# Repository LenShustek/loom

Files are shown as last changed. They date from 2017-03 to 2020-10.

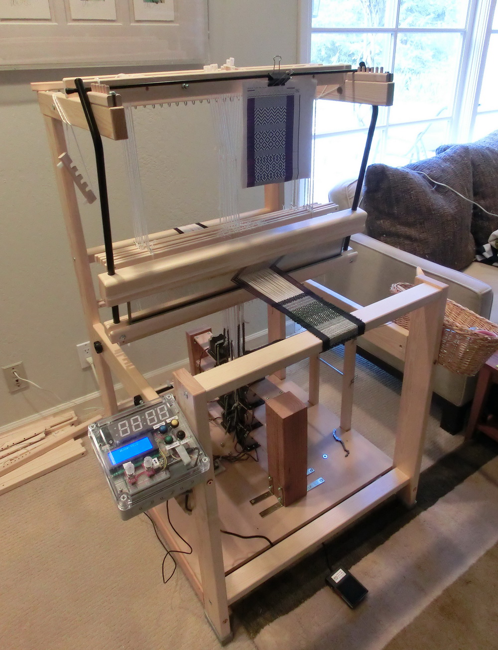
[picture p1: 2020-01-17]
small_weaving_test.JPG

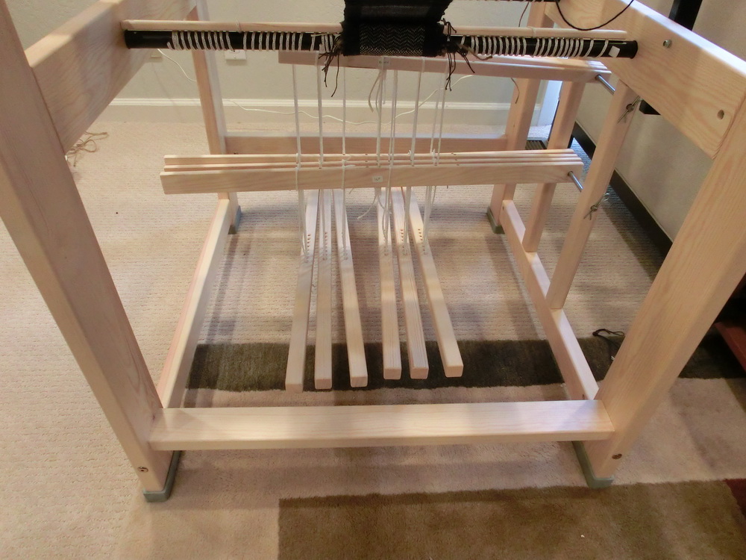
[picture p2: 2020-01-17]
treadles_and_lamms.JPG

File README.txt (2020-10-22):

eLoom: an automation system for the Glimakra "Julia" floor loom 

Tying up a loom with treadles and lamms is complicated, and so is the weaving. 
So I have replaced all the treadles and lamms in our Glimakra "Julia" 
countermarche floor loom with stepper motors that independently operate up to 
8 shafts. That not only makes setup and weaving easier, but it also allows 
patterns that would otherwise not be possible. 

The tie-ups and treadle sequences for up to 16 simulated treadles are 
graphically configured on a small screen. You then weave by throwing the 
shuttle and just pushing the single foot pedal to get the next configuration 
of the shafts. The warping, though, must still be done manually! 

For a one-minute video of it in action, see https://www.youtube.com/watch?v=ygZEDzQJMSk

The hardware added to the loom consists of:
 - up to 8 stepper motors, 23HS22-1504S, NEMA 23, 5.4V, 1.5A, 164 oz-in holding torque
 - up to 8 DRV8825 stepper motor drivers (Pololu or equiv.)
 - a 24VDC 200W power supply
 - 25-pitch sprockets and roller chain to connect the motors to the shaft lines
 - a control box that contains:
   - 1 4-row x 20-character LCD display (Adafruit 198)
   - 1 4-digit 7-segment I2C big digit numerical display (Adafruit 1268)
   - 2 rotary encoders with RGB LEDs and pushbuttons (Sparkfun COM-10982 and BOB-11722)
   - 4 general-purpose pushbuttons (MPJA 32730 or equiv.)
   - 1 attached foot pedal (MPJA 18150 or equiv.)
   - 1 Teensy 3.5 microprocessor, with 512KB flash, 192KB RAM, 4KB EEPROM, and 40 I/O pins
   
Len Shustek, January 2017

October 2020 update: After yeoman service for 3+ years, the plug-in breadboards with the
motor drivers started failing because the high current had deteriorated the contacts.
So I designed a proper printed circuit board replacement that is working great.
The design is in the motordriver subdirectory of this repository.

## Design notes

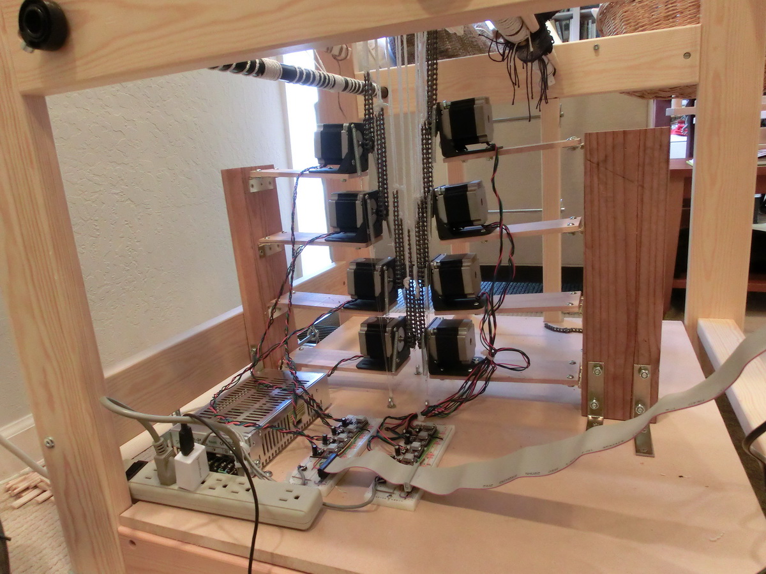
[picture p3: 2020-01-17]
stepper_motors.JPG

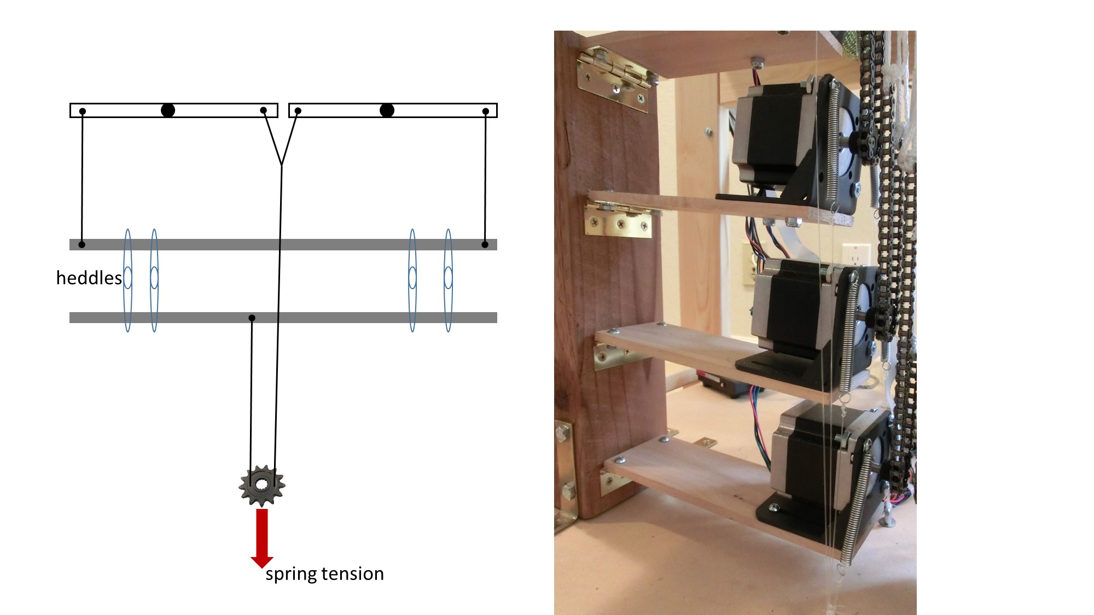
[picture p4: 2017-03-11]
countermarch_action_motorized.jpg

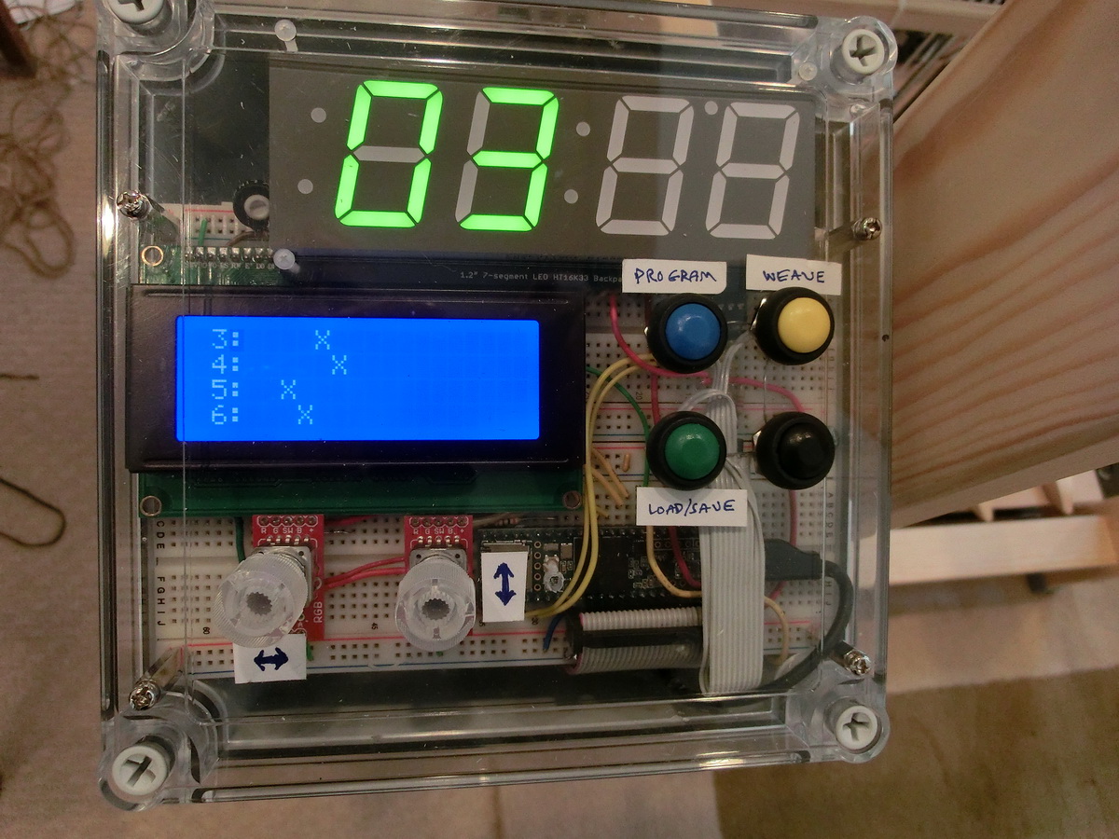
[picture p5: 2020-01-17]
control_box.JPG

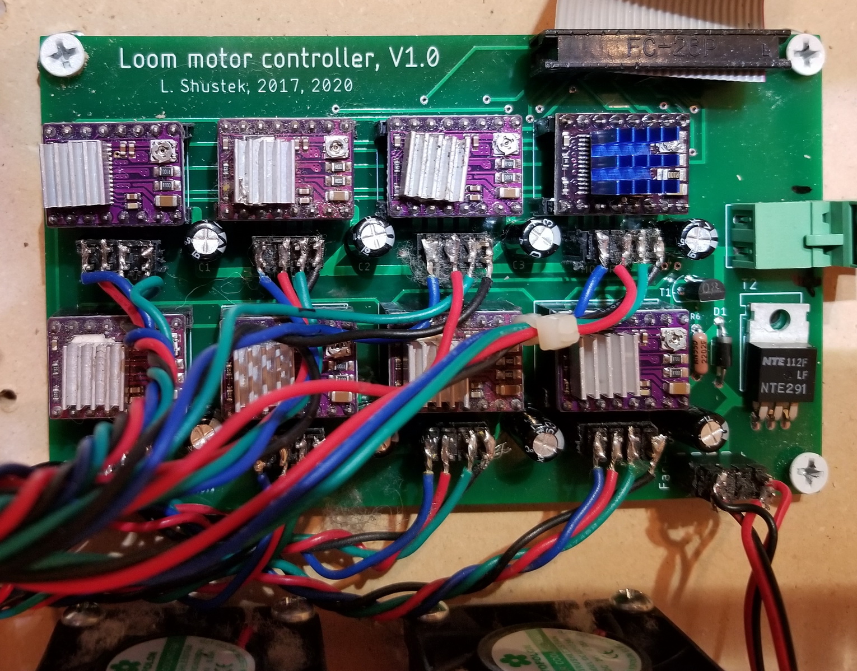
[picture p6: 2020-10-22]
motordriver/motordriver_board.jpg

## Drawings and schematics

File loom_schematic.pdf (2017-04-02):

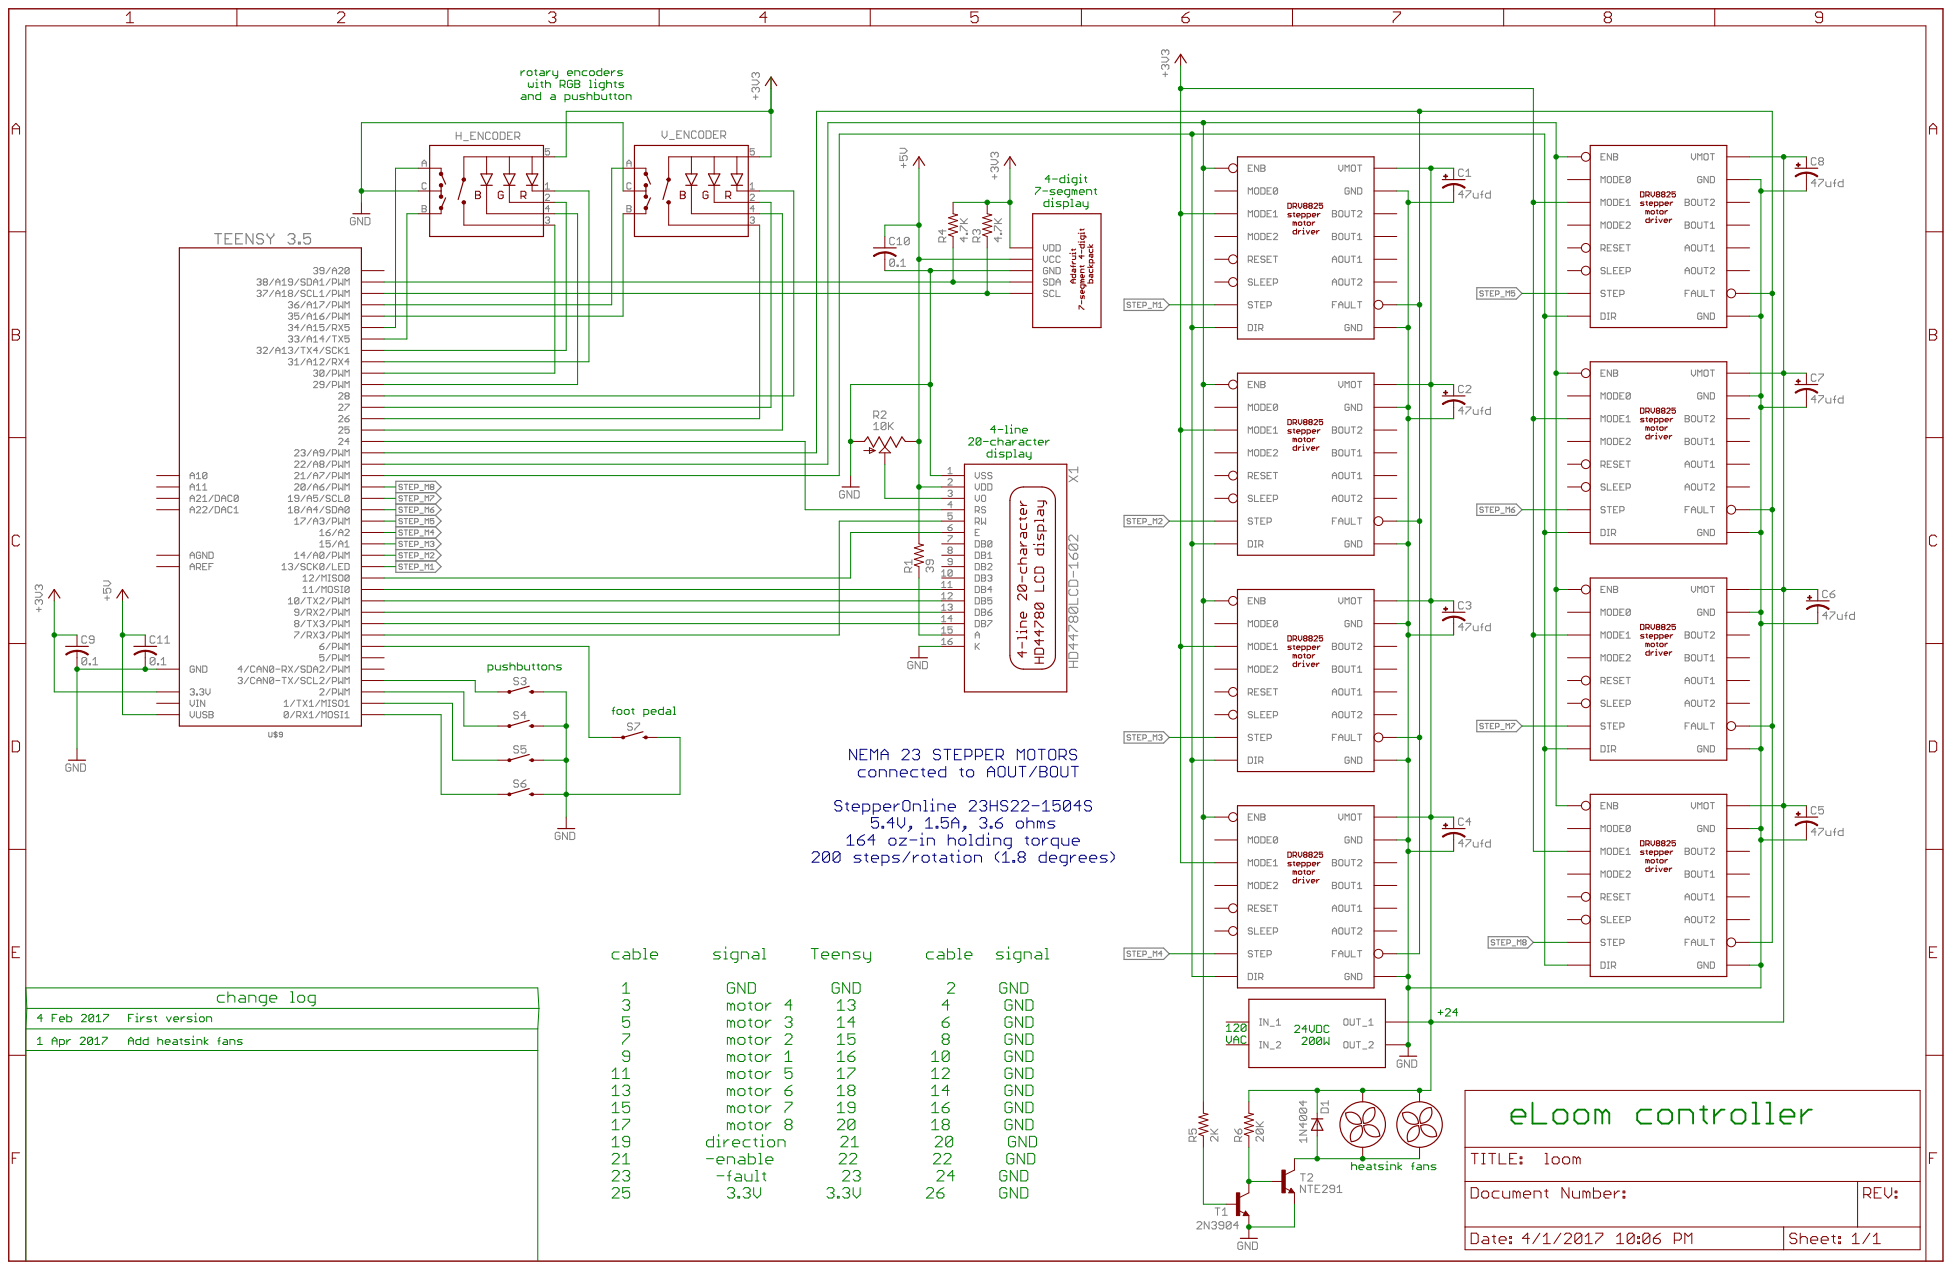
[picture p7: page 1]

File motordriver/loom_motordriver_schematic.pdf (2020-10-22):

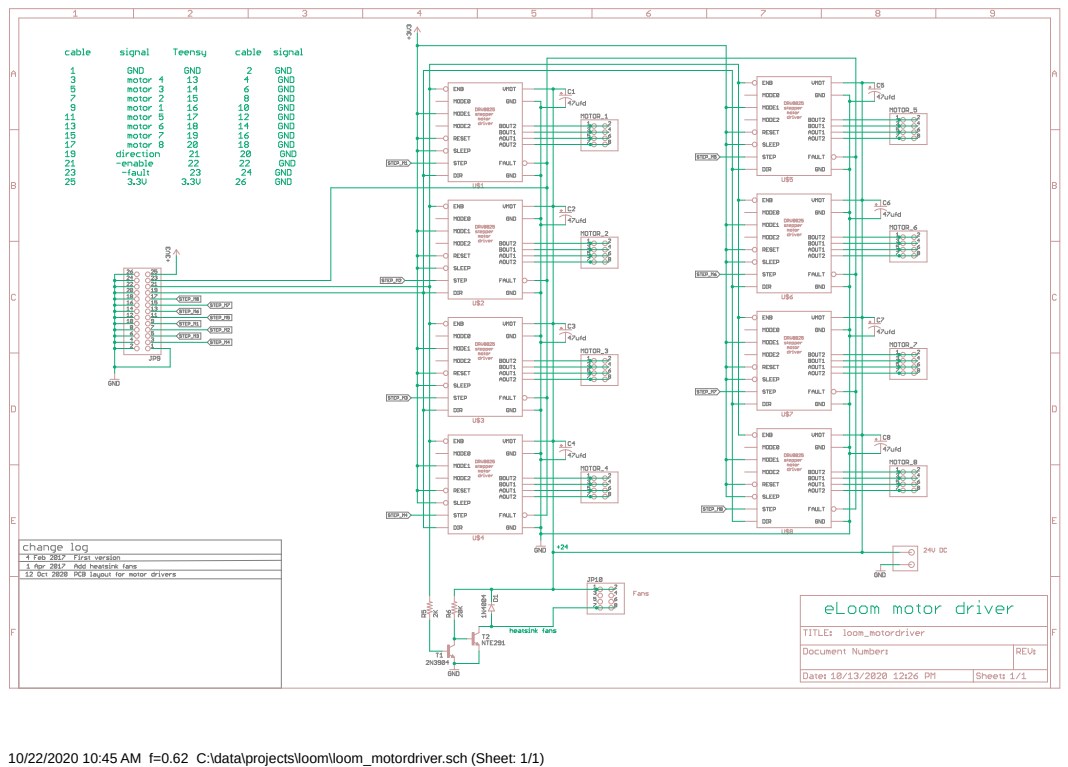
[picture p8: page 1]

10/22/2020 10:45 AM f=0.62 C:\data\projects\loom\loom_motordriver.sch (Sheet: 1/1)

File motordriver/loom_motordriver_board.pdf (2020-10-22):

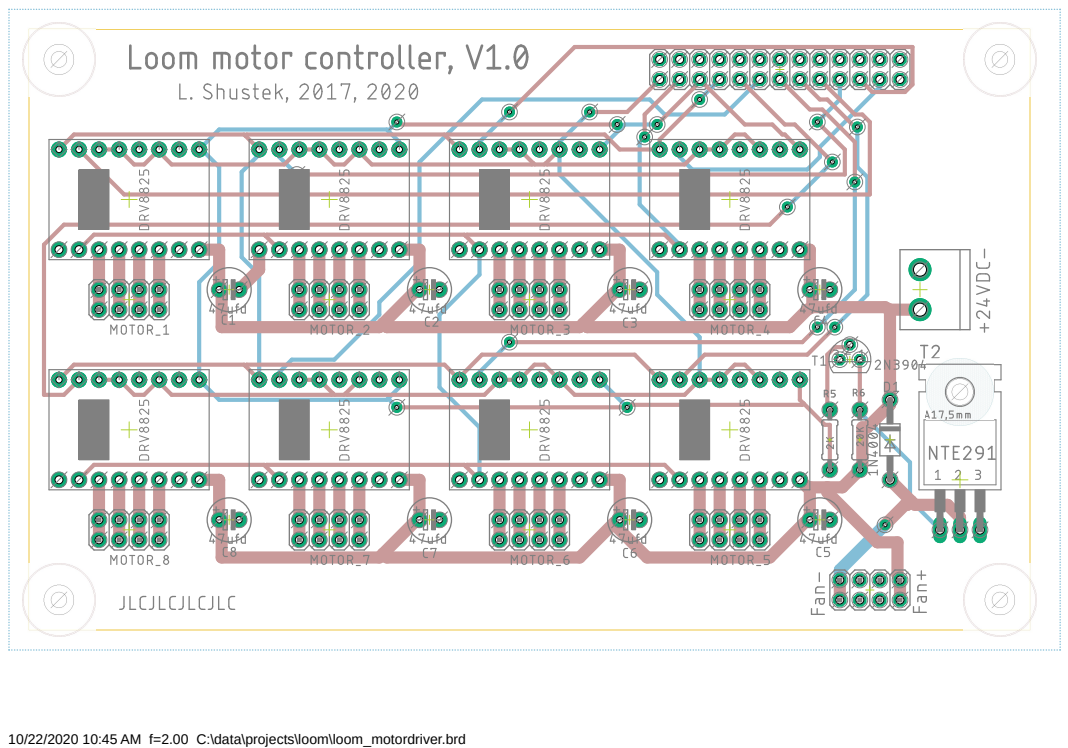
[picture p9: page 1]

10/22/2020 10:45 AM f=2.00 C:\data\projects\loom\loom_motordriver.brd

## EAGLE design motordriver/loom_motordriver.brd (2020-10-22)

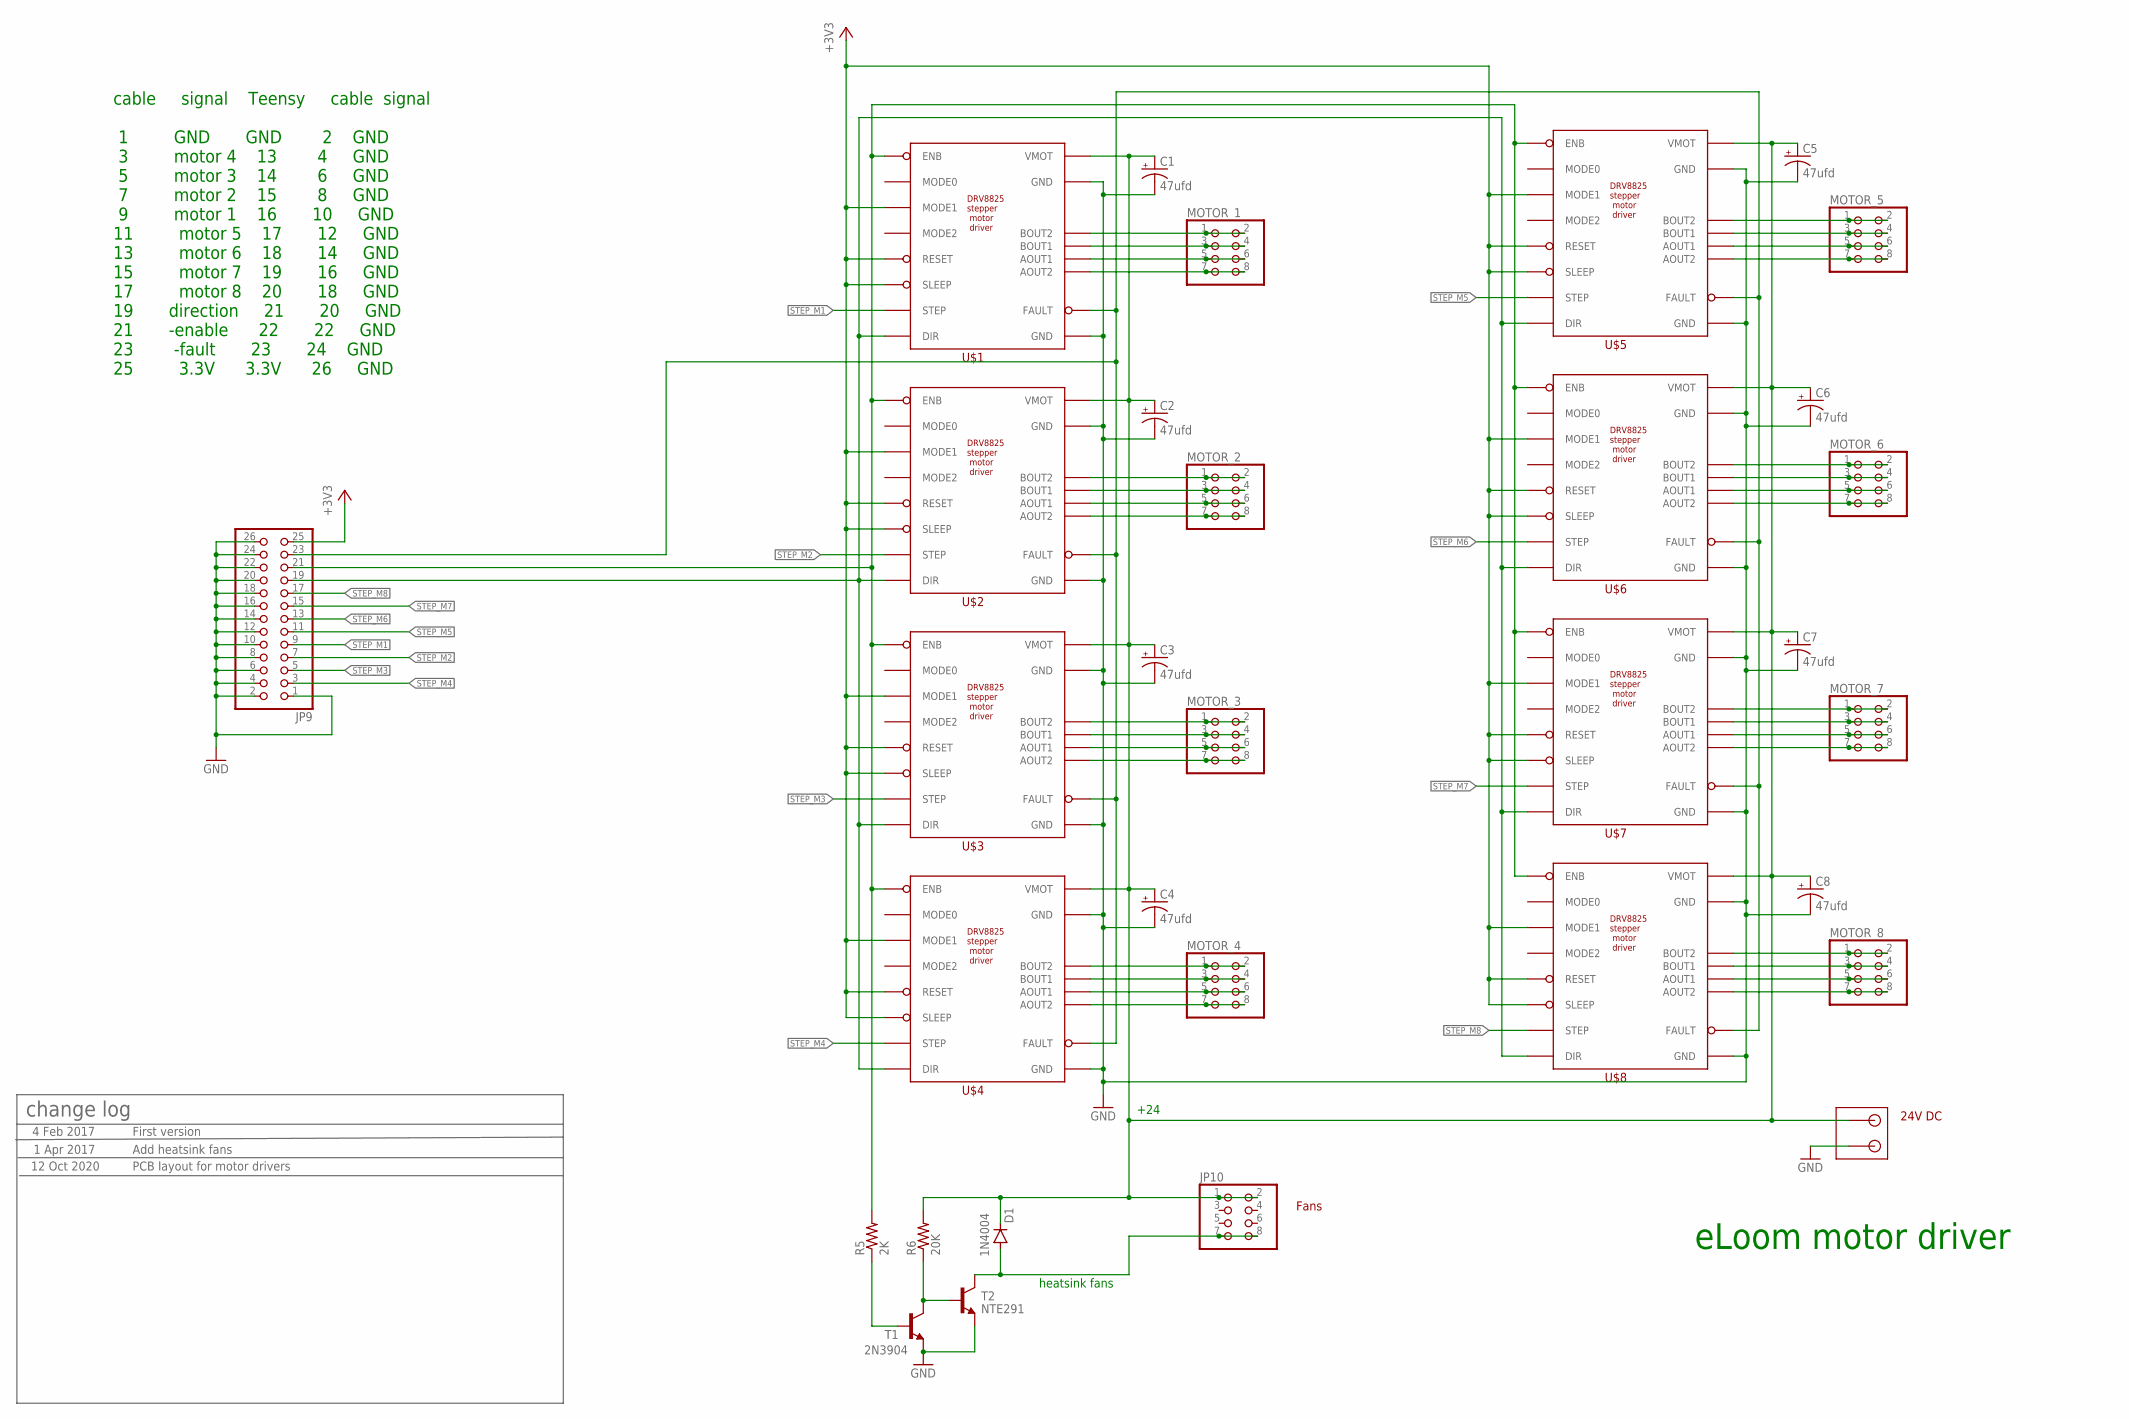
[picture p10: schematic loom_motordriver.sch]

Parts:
C1, C2, C3, C4, C5, C6, C7, C8: 47ufd; E2,5-6
D1: 1N4004; DO41-10
JP9: PINHD-2X13; 2X13
JP10: PINHD-2X4; 2X04
MOTOR_1, MOTOR_2, MOTOR_3, MOTOR_4, MOTOR_5, MOTOR_6, MOTOR_7, MOTOR_8: PINHD-2X4; 2X04
R5: 2K; 0204/7
R6: 20K; 0204/7
T1: 2N3904; TO92
T2: NTE291; TO220
U$1, U$2, U$3, U$4, U$5, U$6, U$7, U$8: DRV8825_STEPPER_MOTOR_DRIVER
U$9: CONNECTOR-2PIN; CONNECTOR-2PIN-5MM

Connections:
24V: C1.+, C2.+, C3.+, C4.+, C5.+, C6.+, C7.+, C8.+, D1.C, JP10.1, JP10.2, R6.2, U$1.P$16 (VMOT), U$2.P$16 (VMOT), U$3.P$16 (VMOT), U$4.P$16 (VMOT), U$5.P$16 (VMOT), U$6.P$16 (VMOT), U$7.P$16 (VMOT), U$8.P$16 (VMOT), U$9.P$1
+3V3: JP9.25, U$1.P$3 (MODE1), U$1.P$5 (RESET), U$1.P$6 (SLEEP), U$2.P$3 (MODE1), U$2.P$5 (RESET), U$2.P$6 (SLEEP), U$3.P$3 (MODE1), U$3.P$5 (RESET), U$3.P$6 (SLEEP), U$4.P$3 (MODE1), U$4.P$5 (RESET), U$4.P$6 (SLEEP), U$5.P$3 (MODE1), U$5.P$5 (RESET), U$5.P$6 (SLEEP), U$6.P$3 (MODE1), U$6.P$5 (RESET), U$6.P$6 (SLEEP), U$7.P$3 (MODE1), U$7.P$5 (RESET), U$7.P$6 (SLEEP), U$8.P$3 (MODE1), U$8.P$5 (RESET), U$8.P$6 (SLEEP)
DIR: JP9.19, U$1.P$8 (DIR), U$2.P$8 (DIR), U$3.P$8 (DIR), U$4.P$8 (DIR), U$5.P$8 (DIR), U$6.P$8 (DIR), U$7.P$8 (DIR), U$8.P$8 (DIR)
ENB: JP9.21, R5.2, U$1.P$1 (ENB), U$2.P$1 (ENB), U$3.P$1 (ENB), U$4.P$1 (ENB), U$5.P$1 (ENB), U$6.P$1 (ENB), U$7.P$1 (ENB), U$8.P$1 (ENB)
FAN: D1.A, JP10.7, JP10.8, T2.2 (C)
FAULT: JP9.23, U$1.P$10 (FAULT), U$2.P$10 (FAULT), U$3.P$10 (FAULT), U$4.P$10 (FAULT), U$5.P$10 (FAULT), U$6.P$10 (FAULT), U$7.P$10 (FAULT), U$8.P$10 (FAULT)
GND: C1.-, C2.-, C3.-, C4.-, C5.-, C6.-, C7.-, C8.-, JP9.1, JP9.2, JP9.4, JP9.6, JP9.8, JP9.10, JP9.12, JP9.14, JP9.16, JP9.18, JP9.20, JP9.22, JP9.24, JP9.26, T1.3 (E), T2.3 (E), U$1.P$9 (GND), U$1.P$15 (GND), U$2.P$9 (GND), U$2.P$15 (GND), U$3.P$9 (GND), U$3.P$15 (GND), U$4.P$9 (GND), U$4.P$15 (GND), U$5.P$9 (GND), U$5.P$15 (GND), U$6.P$9 (GND), U$6.P$15 (GND), U$7.P$9 (GND), U$7.P$15 (GND), U$8.P$9 (GND), U$8.P$15 (GND), U$9.P$2
unnamed: MOTOR_5.1, MOTOR_5.2, U$5.P$14 (BOUT2)
unnamed: MOTOR_5.3, MOTOR_5.4, U$5.P$13 (BOUT1)
unnamed: MOTOR_5.5, MOTOR_5.6, U$5.P$12 (AOUT1)
unnamed: MOTOR_5.7, MOTOR_5.8, U$5.P$11 (AOUT2)
unnamed: MOTOR_6.1, MOTOR_6.2, U$6.P$14 (BOUT2)
unnamed: MOTOR_6.3, MOTOR_6.4, U$6.P$13 (BOUT1)
unnamed: MOTOR_6.5, MOTOR_6.6, U$6.P$12 (AOUT1)
unnamed: MOTOR_6.7, MOTOR_6.8, U$6.P$11 (AOUT2)
unnamed: MOTOR_7.1, MOTOR_7.2, U$7.P$14 (BOUT2)
unnamed: MOTOR_7.3, MOTOR_7.4, U$7.P$13 (BOUT1)
unnamed: MOTOR_7.5, MOTOR_7.6, U$7.P$12 (AOUT1)
unnamed: MOTOR_7.7, MOTOR_7.8, U$7.P$11 (AOUT2)
unnamed: MOTOR_8.1, MOTOR_8.2, U$8.P$14 (BOUT2)
unnamed: MOTOR_8.3, MOTOR_8.4, U$8.P$13 (BOUT1)
unnamed: MOTOR_8.5, MOTOR_8.6, U$8.P$12 (AOUT1)
unnamed: MOTOR_8.7, MOTOR_8.8, U$8.P$11 (AOUT2)
unnamed: MOTOR_1.1, MOTOR_1.2, U$1.P$14 (BOUT2)
unnamed: MOTOR_1.3, MOTOR_1.4, U$1.P$13 (BOUT1)
unnamed: MOTOR_1.5, MOTOR_1.6, U$1.P$12 (AOUT1)
unnamed: MOTOR_1.7, MOTOR_1.8, U$1.P$11 (AOUT2)
unnamed: MOTOR_2.1, MOTOR_2.2, U$2.P$14 (BOUT2)
unnamed: MOTOR_2.3, MOTOR_2.4, U$2.P$13 (BOUT1)
unnamed: MOTOR_2.5, MOTOR_2.6, U$2.P$12 (AOUT1)
unnamed: MOTOR_2.7, MOTOR_2.8, U$2.P$11 (AOUT2)
unnamed: MOTOR_3.1, MOTOR_3.2, U$3.P$14 (BOUT2)
unnamed: MOTOR_3.3, MOTOR_3.4, U$3.P$13 (BOUT1)
unnamed: MOTOR_3.5, MOTOR_3.6, U$3.P$12 (AOUT1)
unnamed: MOTOR_3.7, MOTOR_3.8, U$3.P$11 (AOUT2)
unnamed: R5.1, T1.2 (B)
unnamed: R6.1, T1.1 (C), T2.1 (B)
unnamed: MOTOR_4.1, MOTOR_4.2, U$4.P$14 (BOUT2)
unnamed: MOTOR_4.3, MOTOR_4.4, U$4.P$13 (BOUT1)
unnamed: MOTOR_4.5, MOTOR_4.6, U$4.P$12 (AOUT1)
unnamed: MOTOR_4.7, MOTOR_4.8, U$4.P$11 (AOUT2)
STEP_M1: JP9.9, U$1.P$7 (STEP)
STEP_M2: JP9.7, U$2.P$7 (STEP)
STEP_M3: JP9.5, U$3.P$7 (STEP)
STEP_M4: JP9.3, U$4.P$7 (STEP)
STEP_M5: JP9.11, U$5.P$7 (STEP)
STEP_M6: JP9.13, U$6.P$7 (STEP)
STEP_M7: JP9.15, U$7.P$7 (STEP)
STEP_M8: JP9.17, U$8.P$7 (STEP)

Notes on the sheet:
eLoom motor driver
cable signal Teensy cable signal 1 GND GND 2 GND 3 motor 4 13 4 GND 5 motor 3 14 6 GND 7 motor 2 15 8 GND 9 motor 1 16 10 GND 11 motor 5 17 12 GND 13 motor 6 18 14 GND 15 motor 7 19 16 GND 17 motor 8 20 18 GND 19 direction 21 20 GND 21 -enable 22 22 GND 23 -fault 23 24 GND 25 3.3V 3.3V 26 GND
heatsink fans
+24
change log
4 Feb 2017
First version
1 Apr 2017
Add heatsink fans
24V DC
Fans
12 Oct 2020
PCB layout for motor drivers

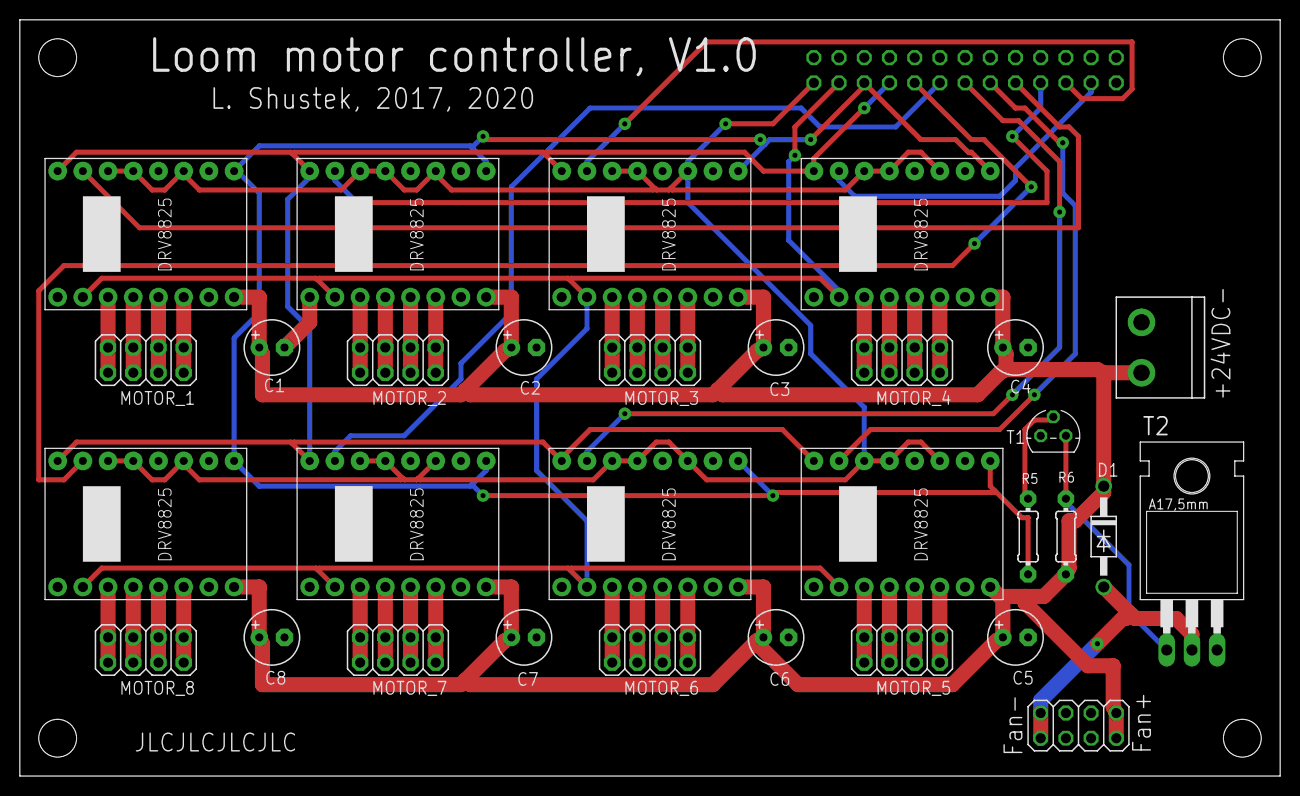
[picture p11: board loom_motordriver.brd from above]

Board: 2 copper layers, 127.0 x 76.2 mm, 32 parts (1 on the bottom side), 49 nets.

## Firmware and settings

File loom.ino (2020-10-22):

/******************************************************************************************************

   automation program for the Glimakra "Julia" floor loom

   The hardware added to the loom consists of:
    - up to 8 stepper motors, 23HS22-1504S, NEMA 23, 5.4V, 1.5A, 164 oz-in holding torque
    - up to 8 DRV8825 stepper motor drivers (Pololu or equiv.)
    - 1 24VDC 200W power supply
    - 1 4-row x 20-character LCD display (Adafruit 198)
    - 1 4-digit 7-segment I2C big digit numerical display (Adafruit 1268)
    - 2 rotary encoders with RGB LEDs and pushbuttons (Sparkfun COM-10982 and BOB-11722)
    - 4 general-purpose pushbuttons (MPJA 32730 or equiv.)
    - 1 foot pedal (MPJA 18150 or equiv.)
    - 1 Teensy 3.5 microprocessor, with 512KB flash, 192KB RAM, 4KB EEPROM, and 40 I/O pins

   The software allows you to graphically configure the treadle tie-ups and the treadle sequence,
   and then weave by throwing the shuttle and just pushing the single foot pedal to get the
   next configuration of the shafts.  The warping, though, must still be done manually!

   See https://github.com/LenShustek/loom for more information about this project.

   When you install a DRV8825 stepper motor driver, adjust the pot on the board so that
   there is 0.75V at the body of the pot, which is for 1.5A drive current to the motor.
   The motor doesn't have to be on when you that.

   ------------------------------------------------------------------------------------------------------
   Copyright (c) 2017, Len Shustek

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
   THE SOFTWARE IS PROVIDED "AS IS", WITHOUT WARRANTY OF ANY KIND, EXPRESS OR IMPLIED, INCLUDING BUT
   NOT LIMITED TO THE WARRANTIES OF MERCHANTABILITY, FITNESS FOR A PARTICULAR PURPOSE AND
   NONINFRINGEMENT. IN NO EVENT SHALL THE AUTHORS OR COPYRIGHT HOLDERS BE LIABLE FOR ANY CLAIM,
   DAMAGES OR OTHER LIABILITY, WHETHER IN AN ACTION OF CONTRACT, TORT OR OTHERWISE, ARISING
   FROM, OUT OF OR IN CONNECTION WITH THE SOFTWARE OR THE USE OR OTHER DEALINGS IN THE SOFTWARE.
   ------------------------------------------------------------------------------------------------------

******************************************************************************************************/
/*
   23 Jan 2017, L. Shustek, V1.0, - first version
   31 Jan 2017, L. Shustek, V1.1, - fix treadle sequence changes during weaving
                                  - clean up filename handling and display
    4 Feb 2017, L. Shustek, V1.2  - add motor fault detection
                                  - fix filename bug
                                  - change schematic to match driver physical layout
                                  - clean up compiler warnings
   10 Feb 2017, L. Shustek, V1.3  - separate motor hardware config, and don't write it to memory
                                  - better debugging output
                                  - parametrize CW/CCW motor initialization
                                  - highlight the treadle while weaving, not just the line
   12 Feb 2017, L. Shustek, V1.4  - more interesting light show during weaving
                                  - make the vertical button during weaving be "undo" to the previous shed
                                  - allow abort from load/save/erase menu
   23 Mar 2017, L. Shustek, V1.5  - increase max treadle sequence to 99
                                  - fix bug when editing the filename extends its length
                                  - temporarily disable motors during weaving if there is no activity for a few minutes
   27 Mar 2017, L. Shustek, V1.6  - display filename on top-level screen, or "unsaved" if pgmg changes are made
                                  - default to current file in load/save menu
                                  - exit from program mode if any other button is pushed
   15 Jun 2017, L. Shustek, V1.7  - fix bug: exiting weaving mode after motors had timed out didn't return
                                    the shafts to the neutral position
    8 Jan 2018, L. Shustek, V1.8  - change "zero" button to "backup" button in weave mode
                                  - display frame numbers instead of X on the tieup screen
                                  - display treadle numbers instead of X on the treadle sequence screen
                                  - fix bug: backing up weave at the first treadle position failed
   28 Oct 2018, L. Shustek, V1.9  - add an option to do "Tabby" between each step of a treadle sequence
                                    if the first two treadles are otherwise unused
    3 Jan 2019, L. Shustek, V1.10 - during calibration, show the distance the frame moves
                                  - add a file option to reverse the fabric by inverting the tieups
   13 Jun 2020, L. Shustek, V1.11 - fix bug: "alternate tabby" wasn't working for shafts other than 0 and 1
                                  - fix bug: always set FILE_TABBY one way or the other when changing programming
   10 Oct 2020, L. Shustek, V1.12 - allow "weave" button to abort the calibration process
                                  - during calibration, show the previously set calibration point
                                  - increase debounce delay because our switches are really noisy

*/
#define VERSION "1.12"

/***** Enhancement ideas:

    - Invent a more programmatic way to configure treadle sequences with repeat loops.
      Since weaving is limited to one treadle at a time we can use decimal rather than unary
      notation on the narrow display. It doesn't match weaving books, though, so weavers would
      consider that sacrilegious!

      Idea #1: a programming mode for "treadle loops", in addition to the traditional sequence.
      The notation might be like this, using "Irish Meadows blanket" as an example:
          4x: 5 6
          6x: 6 5
          8x: 5 6
          ?x: 1 2 3 4
          8x: 5 6
          6x: 6 5
          4x: 5 6
      When weaving, the "?x" line would be repeated indefinitely until a button is pushed to advance.
      Either this "treadle loop" notation or a reconstructed "treadle sequence" notation could be displayed.
      The 3rd and 4th numbers on the big-digit display could show how far along in a repeat sequence we are.
      The file format would have to be elaborated to save and load these looped treadle sequences.

    - Save space by making the tieup[][] matrix be a true bitmap. That would allow more files in the EEPROM.
      Or instead: use an SD card for files, and to hell with optimizing the size to fit in the 4K EEPROM!
*/

#define DEBUG false
#define HW_TEST false

#include <Encoder.h>
#include <LiquidCrystalFast.h>
#include <EEPROM.h>
#include <i2c_t3.h>
#include <string.h>

//**** global parameters

// All stored files will break if NUM_TREADLES, NUM_SHAFTS, or MAX_SEQUENCE is changed!
#define NUM_TREADLES 16 // max 17 will fit on the display currently
#define NUM_SHAFTS 8
#define MAX_SEQUENCE 99

#define MSEC_PER_ROTATION 1000      // how long we should take for one rotation
#define uSTEPS_PER_STEP 4           // how many microsteps per step the drivers are configured for (MODE1 high)
#define STEPS_PER_ROTATION (200 * uSTEPS_PER_STEP)  // the stepper motors have 1.8 degree "full" steps; 360/1.8=200
#define HUNDRETHINCHES_PER_ROTATION ((int)(0.75*3.14*100.0+0.5))  // we use a 3/4" drive gear
#define MIN_STEP_uSEC (1000UL * MSEC_PER_ROTATION / STEPS_PER_ROTATION)
#define DEBOUNCE_MSEC 100
#define ROTATION_PERCENT (130/2) // what part of a full rotation goes from CENTER to UP or DOWN, nominally
#define STEPS_PER_LIGHT_CHANGE 64
#define MINS_BEFORE_MOTOR_DISABLE 10

//**** hardware pin configuration

#define LCD_D4 11  // Hitachi HD44780 LCD controller
#define LCD_D5 10
#define LCD_D6 9
#define LCD_D7 8
#define LCD_ENB 12
#define LCD_RS 24
#define LCD_RW 7
#define PB1 3  // pushbuttons: active low (blue)
#define PB2 2  //   (yellow)
#define PB3 1  //   (green)
#define PB4 0  //   (black)
#define PEDAL 6
#define MOTOR_DIR 21    // direction control for all motors
#define MOTOR_ENB 22    // active low: enable motors
#define MOTOR_FAULT 23  // active low input: motor fault
#define H_ENC_RED 31    // horizontal and vertical rotary encoder lights
#define H_ENC_GREEN 32  //   (active low)
#define H_ENC_BLUE 29
#define V_ENC_RED 28
#define V_ENC_GREEN 27
#define V_ENC_BLUE 25
#define LED_ON LOW
#define LED_OFF HIGH
#define H_ENC_PB 30     // encoder pushbuttons: active high
#define V_ENC_PB 26
#define H_ENC_A 34      // encoder step outputs
#define H_ENC_B 33
#define V_ENC_A 36
#define V_ENC_B 35
#define ENCODER_INCR 4  // number of encoder steps per click
#define LED_SCL 37      // SCL1 for the big 4-digit 7-segment LED display (Wire1)
#define LED_SDA 38      // SDA1 for the big 4-digit 7-segment LED display (Wire1)
#define I2C_ADDR 0x70   // default I2C slave address
// unused Teensy 3.5 pins: 4, 5, 39

enum events { // input events
   eNone,
   ePB1, ePB2, ePB3, ePB4,  // big pushbuttons: program, weave, load/save, unweave
   ePBH, ePBV,              // horizontal and vertical encoder pushbuttons
   ePEDAL,                  // foot pedal
   eHrotL, eHrotR,          // horizontal encoder rotation
   eVrotL, eVrotR           // vertical encoder rotation
};
static struct {   // input pins
   byte pin;
   enum events event;
   byte active_state; }
inpins[] = {
   {PB1, ePB1, LOW },
   {PB2, ePB2, LOW },
   {PB3, ePB3, LOW },
   {PB4, ePB4, LOW },
   { H_ENC_PB, ePBH, HIGH },
   { V_ENC_PB, ePBV, HIGH },
   {PEDAL, ePEDAL, LOW },
   {0xff } };

static byte lightpins[] = { // output pins for encoder LEDs
   H_ENC_RED, H_ENC_GREEN, H_ENC_BLUE,
   V_ENC_RED, V_ENC_GREEN, V_ENC_BLUE, 0xff };

static struct  { // output pins for the stepper motors
   byte pin_step;       // what pin starts a step for this motor
   bool clockwise;      // is clockwise up?
#define FRONT_CW false  // (these depend on which way the chains are
#define BACK_CW true    //  looped around the sprockets)
} shaft_hardware[NUM_SHAFTS] = {
   {16, FRONT_CW }, // top front motor
   {15, FRONT_CW },
   {14, FRONT_CW },
   {13, FRONT_CW }, // bottom front motor
   {17, BACK_CW },  // bottom back motor
   {18, BACK_CW },
   {19, BACK_CW },
   {20, BACK_CW }   // top back motor
};

enum shaft_positions {SHAFT_CENTER, SHAFT_UP, SHAFT_DOWN };
#define NOMINAL_STEPS ((ROTATION_PERCENT * STEPS_PER_ROTATION) / 100)
static struct {
   enum shaft_positions shaft_position;  // where is the shaft currently?
   int steps_to_down;   // how many steps move from center to down
   int steps_to_up;     // how many steps move from center to up
   int steps_to_move;   // how many steps up (pos) or down (neg) are left to move
}
shaft_status[NUM_SHAFTS] = {
   {SHAFT_CENTER,  NOMINAL_STEPS,  NOMINAL_STEPS, 0 },  // top front motor
   {SHAFT_CENTER,  NOMINAL_STEPS,  NOMINAL_STEPS, 0 },
   {SHAFT_CENTER,  NOMINAL_STEPS,  NOMINAL_STEPS, 0 },
   {SHAFT_CENTER,  NOMINAL_STEPS,  NOMINAL_STEPS, 0 },  // bottom front motor
   {SHAFT_CENTER,  NOMINAL_STEPS,  NOMINAL_STEPS, 0 },  // bottom back motor
   {SHAFT_CENTER,  NOMINAL_STEPS,  NOMINAL_STEPS, 0 },
   {SHAFT_CENTER,  NOMINAL_STEPS,  NOMINAL_STEPS, 0 },
   {SHAFT_CENTER,  NOMINAL_STEPS,  NOMINAL_STEPS, 0 }   // top back motor
};

// weaving configuration

static bool tieup [NUM_SHAFTS] [NUM_TREADLES] =  { // does shaft i go down with treadle j?
   // initialization: a line is all treadles connected to a particular shaft
   {1, 0, 0, 0, 0, 0, 0, 0, 0, 0, 0, 0, 0, 0, 0, 0 }, // initialized to basic weave
   {0, 1, 0, 0, 0, 0, 0, 0, 0, 0, 0, 0, 0, 0, 0, 0 },
   /* everything else is 0 */
};
static byte treadle_sequence[MAX_SEQUENCE]; // treadle sequence for this pattern; values are 0..NUM_TREADLES-1
#define UNUSED_SEQ 0xff                     // or 0xff signifying "this position is unused"
static int sequence_size;

//**** EEPROM format for persistent data

#define EEPROM_SIZE 4096
/* layout in the EEPROM is:
     config_hdr
     shaft_status []
     repeat for each file {
        file_hdr
        tieup []
        treadle_sequence []
        }
*/
struct {
   char id[4];       // "cfg" for identification
   int size;         // CONFIG_SIZE: size of the whole config record, including this header
   byte numshafts;   // compile-time config parameters for consistency checking
   byte numtreadles;
   byte maxsequence;
   byte lastfilenum;  // the last file we loaded or saved
   byte tr_seq_pos;   // the current index into the treadle sequence for that file
   byte tr_treadle;   // the current treadle (could be 0/1 for "alternate tabby" mode)
   byte unused[14];
   // after this we write the "shaft_status" array, which contains the current shaft configuration data
} config_hdr = {0 };
#define CONFIG_SIZE ((int)sizeof(config_hdr) + (int)sizeof(shaft_status))

#define MAX_FILENAME 14
struct {
   char id[4]; // "fil" for identification
   int16_t size;   // size of the whole file, including this header
   byte flags;
#define FILE_TABBY 0x01         // use Tabby 1/2 between each treadle step
#define FILE_INVERT_TIEUPS 0x02 // invert the top and bottom of the fabric
   byte unused;
   byte checksum;
   char filename[MAX_FILENAME + 1]; // null-terminated string
   // after this we write the tieup array, followed by the treadle_sequence vector
} file_hdr;
#define FILE_SIZE ((int)sizeof(file_hdr) + (int)sizeof(tieup) + (int)sizeof(treadle_sequence))
#define MAX_FILES ((EEPROM_SIZE - CONFIG_SIZE) / FILE_SIZE)
// The current implementation assumes all files are padded to the fixed maximum size.
// All stored files will break if NUM_SHAFTS, NUM_TREADLES, or MAX_SEQUENCE is changed!

//    other global variables

LiquidCrystalFast lcd (LCD_RS, LCD_RW, LCD_ENB, LCD_D4, LCD_D5, LCD_D6, LCD_D7);
Encoder H_ENC (H_ENC_A, H_ENC_B);
Encoder V_ENC (V_ENC_A, V_ENC_B);
long Hold, Vold;  // last encoder values
#define ENC_STEPS_PER_CLICK 4
char last_filename[MAX_FILENAME + 1] = {0};
bool unsaved_file = false;

//***********************************************************************
//    utility routines
//***********************************************************************

void assert (boolean test, const char *msg) {
   if (!test) {
      lcd.clear(); lcd.print("** INTERNAL ERROR **");
      lcd.setCursor(0, 1); lcd.print("Assertion failed:");
      lcd.setCursor(0, 2); lcd.print(msg);
      while (true) ; } }

void center_message (byte row, const char *msg) {
   int len, nblanks;
   len = strlen(msg);
   assert (len <= 20, "bad center_message");
   nblanks = (20 - len) >> 1;
   lcd.setCursor(0, row);
   for (byte i = 0; i < nblanks; ++i) lcd.print(" ");
   lcd.print(msg);
   nblanks = (20 - nblanks) - len;
   for (byte i = 0; i < nblanks; ++i) lcd.print(" "); }

void info_message(const char *msg1, char *msg2) {
   lcd.clear(); center_message(1, msg1);
   if (msg2) center_message(2, msg2);
   delay(3000);
   lcd.clear(); }

void wait_for_button(byte pin) {
   while (digitalRead(pin) == HIGH) ;
   delay(DEBOUNCE_MSEC);
   while (digitalRead(pin) == LOW) ;
   delay(DEBOUNCE_MSEC); }

void testbutton (byte pin, bool active) {
   if (digitalRead(pin) == active) {
      Serial.print("pushed: "); Serial.println(pin);
      delay(DEBOUNCE_MSEC);
      while (digitalRead(pin) == active) ;
      Serial.print("release: "); Serial.println(pin);
      delay(DEBOUNCE_MSEC); } }

void H_LED (int led) {
   digitalWrite(H_ENC_RED, led == H_ENC_RED ? LED_ON : LED_OFF);
   digitalWrite(H_ENC_GREEN, led == H_ENC_GREEN ? LED_ON : LED_OFF);
   digitalWrite(H_ENC_BLUE, led == H_ENC_BLUE ? LED_ON : LED_OFF); }
void V_LED (int led) {
   digitalWrite(V_ENC_RED, led == V_ENC_RED ? LED_ON : LED_OFF);
   digitalWrite(V_ENC_GREEN, led == V_ENC_GREEN ? LED_ON : LED_OFF);
   digitalWrite(V_ENC_BLUE, led == V_ENC_BLUE ? LED_ON : LED_OFF); }

//***********************************************************************
//     big 7-sgement LED display routines
//***********************************************************************

static const uint8_t numbertable[] = {
   0x3F, /* 0 */  0x06, /* 1 */  0x5B, /* 2 */  0x4F, /* 3 */  0x66, /* 4 */
   0x6D, /* 5 */  0x7D, /* 6 */  0x07, /* 7 */  0x7F, /* 8 */  0x6F, /* 9 */
   0x77, /* a */  0x7C, /* b */  0x39, /* C */  0x5E, /* d */  0x79, /* E */  0x71, /* F */
};
uint16_t displaybuffer[8];

void led7_turnoff(void) {
   Wire1.beginTransmission(I2C_ADDR);
   Wire1.write(0x80);  // turn off the display
   Wire1.endTransmission(); }

void led7_start(void) {
   Wire1.begin();    // start LED display
   Wire1.beginTransmission(I2C_ADDR);
   Wire1.write(0x21);  // turn on oscillator
   Wire1.endTransmission();
   Wire1.beginTransmission(I2C_ADDR);
   Wire1.write(0xef);  // set maximum brightness
   Wire1.endTransmission();
   led7_turnoff(); }

void led7_write_digit(byte pos, byte num, bool dot) {
   if (pos > 4) pos = 4;
   if (num > 15) num = 15;
   displaybuffer[pos] = numbertable[num] | (dot << 7); }

void led7_shownum(byte num, bool left) {
   led7_write_digit(left ? 0 : 3, (num / 10) % 10, false);
   led7_write_digit(left ? 1 : 4, num % 10, false);
   Wire1.beginTransmission(I2C_ADDR);
   Wire1.write((uint8_t)0x00); // start at address $00
   for (uint8_t i = 0; i < 8; i++) {
      Wire1.write(displaybuffer[i] & 0xFF);
      Wire1.write(displaybuffer[i] >> 8); }
   Wire1.endTransmission();
   Wire1.beginTransmission(I2C_ADDR);
   Wire1.write(0x81);  // turn on the display
   Wire1.endTransmission(); }

//****** more utility routines

void test_hardware(void) {
   for (int i = 0; lightpins[i] != 0xff; ++i) { // test all the lights
      digitalWrite(lightpins[i], LOW);
      delay(750);
      digitalWrite(lightpins[i], HIGH);
      delay(250); }
   for (int row = 0; row < 4; ++row) {  // test the LCD display
      char buf[21];
      sprintf(buf, "row %d", row);
      center_message(row, buf); }
   for (int leftright = 0; leftright < 2; ++leftright) {
      for (int i = 0; i < 10; ++i) { // test the LED display
         led7_shownum(i, leftright);
         delay(500); }
      for (int i = 0; i < 100; i += 10) {
         led7_shownum(i, leftright);
         delay(500); } }
   long Vold = -999, Hold = -999, Vnew, Hnew;
   while (1) {
      testbutton(PB1, LOW);
      testbutton(PB2, LOW);
      testbutton(PB3, LOW);
      testbutton(PB4, LOW);
      testbutton(PEDAL, LOW);
      testbutton(H_ENC_PB, HIGH);
      testbutton(V_ENC_PB, HIGH);
      Hnew = H_ENC.read();
      if (Hnew != Hold) {
         Serial.print("H pos: "); Serial.println(Hnew);
         Hold = Hnew; }
      Vnew = V_ENC.read();
      if (Vnew != Vold) {
         Serial.print("V pos: "); Serial.println(Vnew);
         Vold = Vnew; } } }

enum events check_event(void) {
   // check for a switch or button event; return eNone if none
   for (int i = 0; inpins[i].pin != 0xff; ++i) { //test all inputs
      // we should be cleverer here: trigger on press, but record to ignore until release
      if (digitalRead(inpins[i].pin) == inpins[i].active_state) { // button pushed
         delay(DEBOUNCE_MSEC);
         while (digitalRead(inpins[i].pin) == inpins[i].active_state) ;  // wait for release
         delay(DEBOUNCE_MSEC);
         return inpins[i].event; } }
   long Hnew = H_ENC.read();
   if (Hnew - Hold >= ENC_STEPS_PER_CLICK) {
      Hold = Hnew;
      return eHrotL; }
   if (Hold - Hnew >= ENC_STEPS_PER_CLICK) {
      Hold = Hnew;
      return eHrotR; }
   long Vnew = V_ENC.read();
   if (Vnew - Vold >= ENC_STEPS_PER_CLICK) {
      Vold = Vnew;
      return eVrotL; }
   if (Vold - Vnew >= ENC_STEPS_PER_CLICK) {
      Vold = Vnew;
      return eVrotR; }
   return eNone; }

bool wait_yesno(const char *msg1, const char *msg2) {
   enum events event;
   bool answer;
   lcd.clear();
   if (msg1) center_message(0, msg1);
   if (msg2) center_message(1, msg2);
   center_message(3, "  yes       no  ");
   H_LED(H_ENC_GREEN);
   V_LED(V_ENC_RED);
   while (1) {
      event = check_event();
      if (event == ePBH) {
         answer = true;
         break; }
      if (event == ePBV) {
         answer =  false;
         break; } }
   H_LED(0); V_LED(0);
   lcd.clear();
   return answer; }

int ask_choice(const char *msg1, const char *msg2, const char *msg3, const char *msg4) {
   // return 0 if abort, else choice 1..4
   enum events event;
   int row = 0, numchoices = 2, answer = -1;
   lcd.clear();
   center_message(0, msg1);
   center_message(1, msg2);
   if (msg3) {
      center_message(2, msg3);
      ++numchoices;
      if (msg4) {
         center_message(3, msg4);
         ++numchoices; } }
   V_LED(V_ENC_GREEN);
   H_LED(H_ENC_RED);
   while (answer < 0) {
      lcd.setCursor(10, row); // put cursor in the center of the line
      lcd.blink();
      event = check_event();
      switch (event) {
         case eVrotL: // up
            if (row > 0) --row;;
            break;
         case eVrotR: // down
            if (row < numchoices - 1) ++row;
            break;
         case ePBV:  // green button selects a choice
            answer = row + 1;
            break;
         default:
            if (event != eNone) answer = 0;  // any other button aborts
            break; } }
   lcd.noBlink();
   V_LED(0); H_LED(0);
   return answer; }

void lcd_write_dd (int number) {
   lcd.write(number < 10 ? ' ' : '0' + number / 10);
   lcd.write('0' + number % 10);
   lcd.write(':'); }
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
void loop(void) {
   enum events event;
   char string[22];
   lcd.clear();
   sprintf(string, "eLoom V%s", VERSION);
   center_message(0, string);
   center_message(3, unsaved_file ? "<unsaved file>" : last_filename);
   do {
      event = check_event(); }
   while (event == eNone);
   switch (event) {
      case ePB1:
         event = program_tieups();
         if (event == ePB1) program_treadle_sequence();
         break;
      case ePB2:
         weave();
         break;
      case ePB3:
         loadsave_files();
         break;
      default: ; } }
//*

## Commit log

2017-02-11 installed all 8 stepper motors
2017-02-12 add cable signal table
2017-03-11 diagram the motorized countermarch actiion
2017-03-28 various small enhancements and bug fixes
    [loom.ino]
2017-04-02 add circuit to switch heatsink fans on and off
2019-01-03 new features; bug fixes
    [loom.ino]
2020-10-22 minor enhancements and bug fixes
    [loom.ino]
2020-10-22 Made a printed circuit board for the motor drivers
    [loom_motordriver.brd, loom_motordriver.sch]

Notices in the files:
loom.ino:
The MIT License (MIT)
